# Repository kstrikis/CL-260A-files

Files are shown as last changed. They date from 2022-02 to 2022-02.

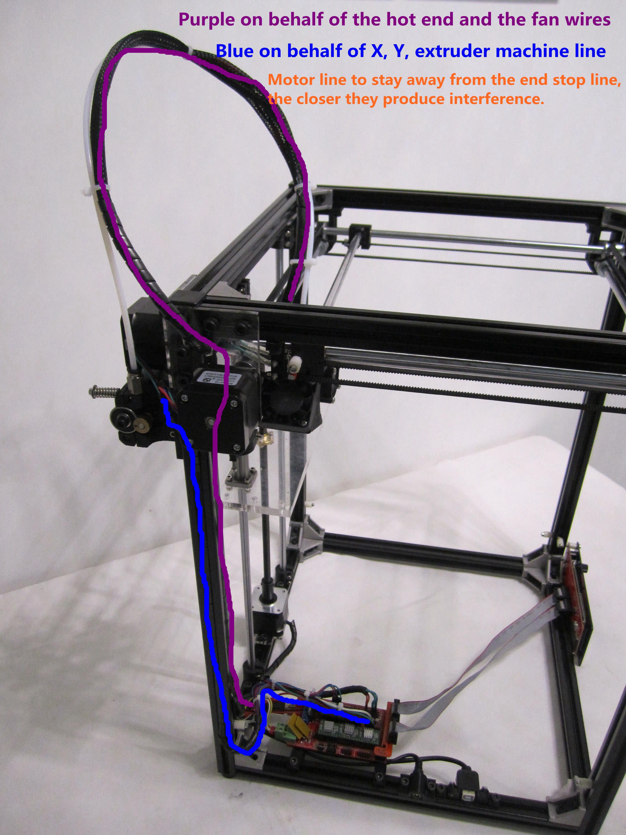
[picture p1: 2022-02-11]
CL-260 manual (original information pack)/Assemble the tutorial/photo/4.JPG

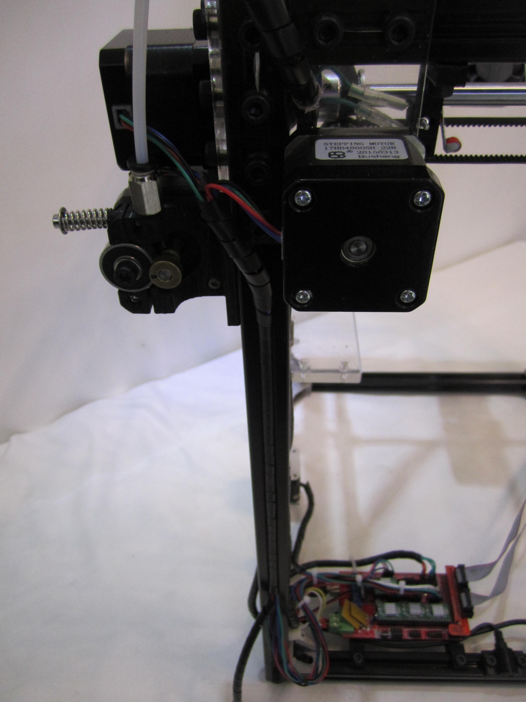
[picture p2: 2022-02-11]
CL-260 manual (original information pack)/Assemble the tutorial/photo/11.JPG

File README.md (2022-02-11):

# CL-260A-files
Files and notes for running an Ultimaker 2 clone 3D printer

Thanks to SirGeekALot for most of the Marlin tweaks.
Notably, my extruder PID settings are very different from his, though.
So you should find your own, with M303 C8 E0 S205 U1
| Original					 | SirGeekALot					 | Mine |
| :---: | :---: | :---: |
| #define  DEFAULT_Kp 22.2	| #define  DEFAULT_Kp 29.79	| #define DEFAULT_Kp  14.06 |
| #define  DEFAULT_Ki 1.08	| #define  DEFAULT_Ki 2.31	| #define DEFAULT_Ki 0.64 |
| #define  DEFAULT_Kd 114	  | #define  DEFAULT_Kd 95.90	| #define DEFAULT_Kd  76.44 |

### To send the tweaked Marlin firmware to your CL-260A:

0. Ensure you have the same hardware, including:
Arduino Mega 2560  
RAMPS 1.4 board  
Heated bed  
A4988 stepper drivers  
128 x 64 LCD screen <-- If you do not have this, comment out line 2378 in Configuration.h:  
    //#define REPRAP_DISCOUNT_FULL_GRAPHIC_SMART_CONTROLLER

1. Install drivers for the CH340 USB-serial chip
	Copies of the driver files are in "CH340 drivers"
	The OEM's drivers page: http://www.wch.cn/download/CH341SER_EXE.html

2. Install Arduino IDE
	https://www.arduino.cc/en/software

3. Test the connection to the Arduino by uploading the blink example program

4. Download Marlin 2.0.x: https://github.com/MarlinFirmware/Marlin
   I used Marlin 2.0.9.3

5. Replace Configuration.h and Configuration_adv.h

6. Run Marlin.ino

7. Upload. This takes several minutes.

8. Run M303 C8 E0 S205 U1 to find your own extruder PID settings.  
	This already saves the settings in EEPROM, but better to keep a copy.  
	Watch the terminal near completion so the temp sensor readings
	don't push the PID tuning output past the end of the log
	before you can read them

9. Add your PID settings to your own copy of Configuration.h

### To use import the Cura settings:

1. Install Cura
	https://ultimaker.com/software/ultimaker-cura
	I used Cura 4.13.1
  
2. Help -> Show Configuration Folder

3. Copy all the files from "cura" into your configuration folder

4. Note that my starting G-code includes a "brush wipe" step
  where you may strap a toothbrush in that corner to wipe the
  nozzle over it before each print.

### CL-260 manual (original information pack) is what the manufacturer provided.
It uses Marlin 1.x (incompatible with 2.x), has a similarly incompatible Cura file.  
They suggest Repetier but with a Raspberry Pi and Octoprint you can untether
the printer from your computer.

### Other changes:
Better 24V power supply  
    Cover for PSU: https://www.thingiverse.com/thing%3a119109  
        https://web.archive.org/web/20161110102835/http://www.thingiverse.com/thing:119109   
        Here is a similar one: https://www.thingiverse.com/thing:40377  
    Bracket for PSU: CL-26_PSU_Bracket.stl  
Add grounding wires to the frame  
Add spool holder that fits onto provided bolt: m5-spool-holder.stl  
Case for 12864 LCD screen: https://www.thingiverse.com/search?q=12864+case&type=things&sort=relevant  
Longer ribbon cables to mount LCD screen on top T-slot frame  
Messy wiring  
Piece of tempered glass that is almost the right size  

### Potential changes:
* Use RAMPS 1.6 board  
* Use better stepper drivers. quieter operation, maybe smoother  
* DRV8825 - do not use. requires TL smoother for use at low speed  
* TMC2130  
* TMC2208  
* TMC2209 - less hot than TMC2208.  
  Support for sensorless homing! Very cool. Maybe it puts too much force on z-axis, though;  
  you don't want to delevel the bed or damage the bed or nozzle.  
  Still, it could potentially allow mesh bed leveling.  
  The TMC2209 uses UART mode for sensorless homing, to use it will require some wiring.  
  You can use one-to-many wiring, where all the stepper motors share a bus and are configured with unique 2-bit addresses  
  The extruder should be run with spreadCycle, axis motors run with stealthChop  
  These two modes are configured by bringing a couple pins to VCC, ground, or leaving them open on the driver

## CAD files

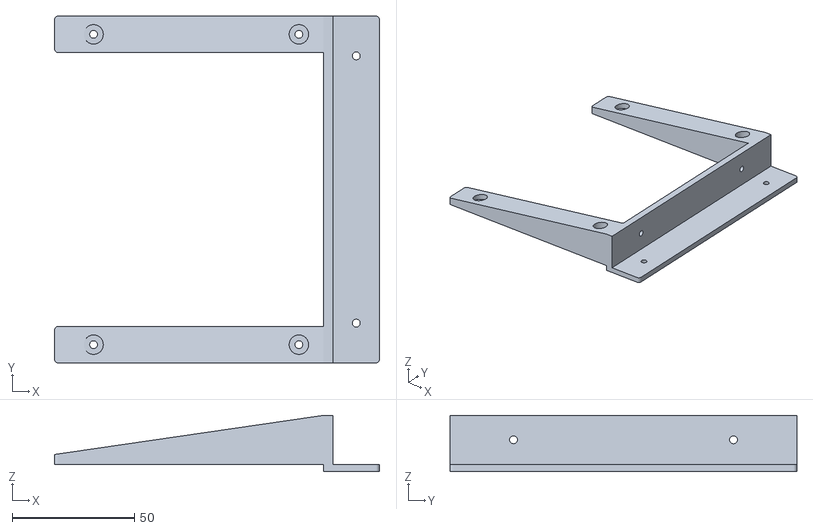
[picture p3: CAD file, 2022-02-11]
parts/CL-26_PSU_Bracket.stl
133.0 x 142.0 x 23.0

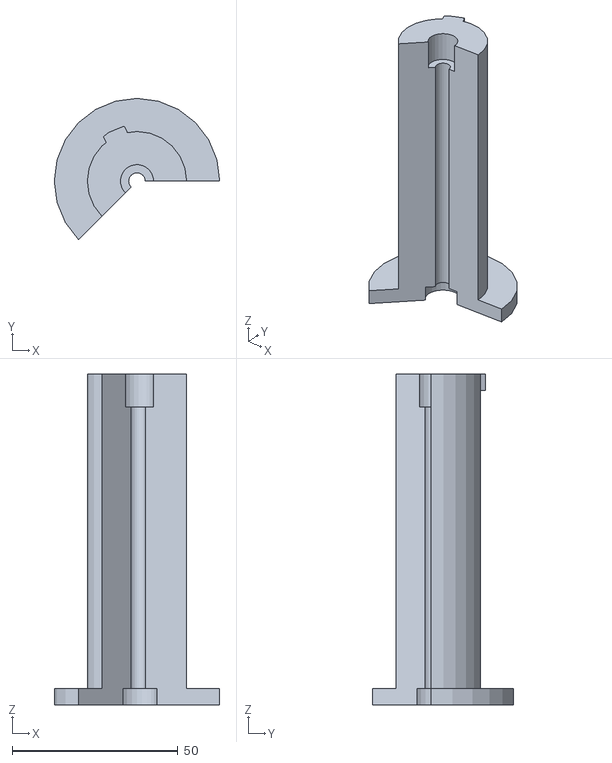
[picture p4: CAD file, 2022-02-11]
parts/m5-spool-holder.stl
50.0 x 42.7 x 100.0

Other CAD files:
parts/m5-spool-holder.skp

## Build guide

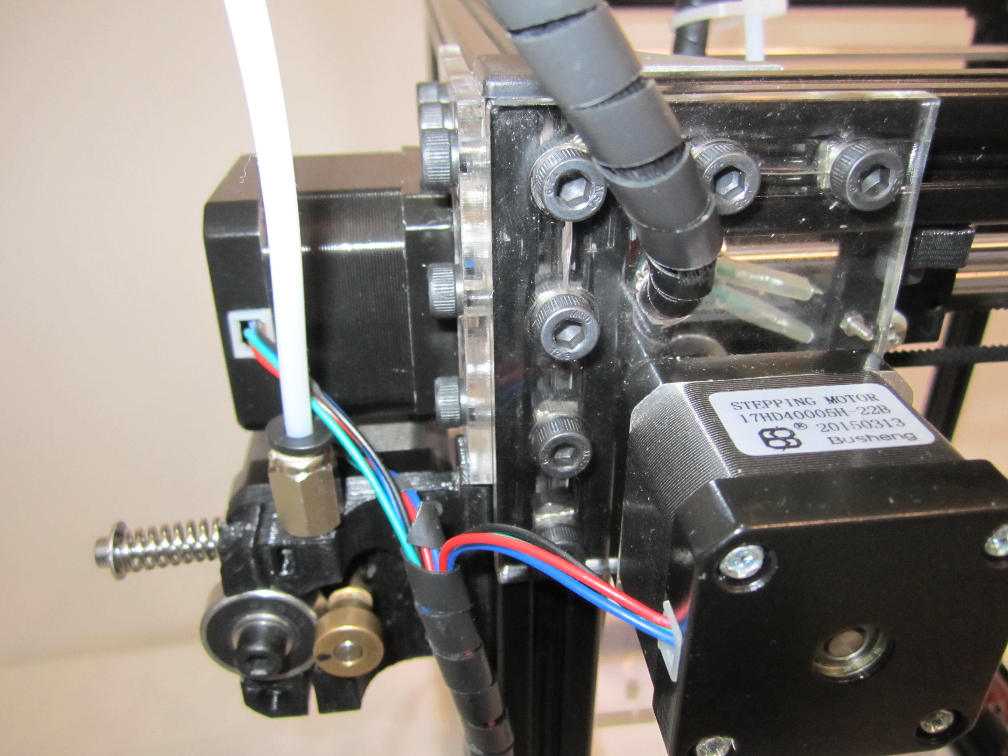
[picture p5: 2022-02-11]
CL-260 manual (original information pack)/Assemble the tutorial/photo/9.JPG

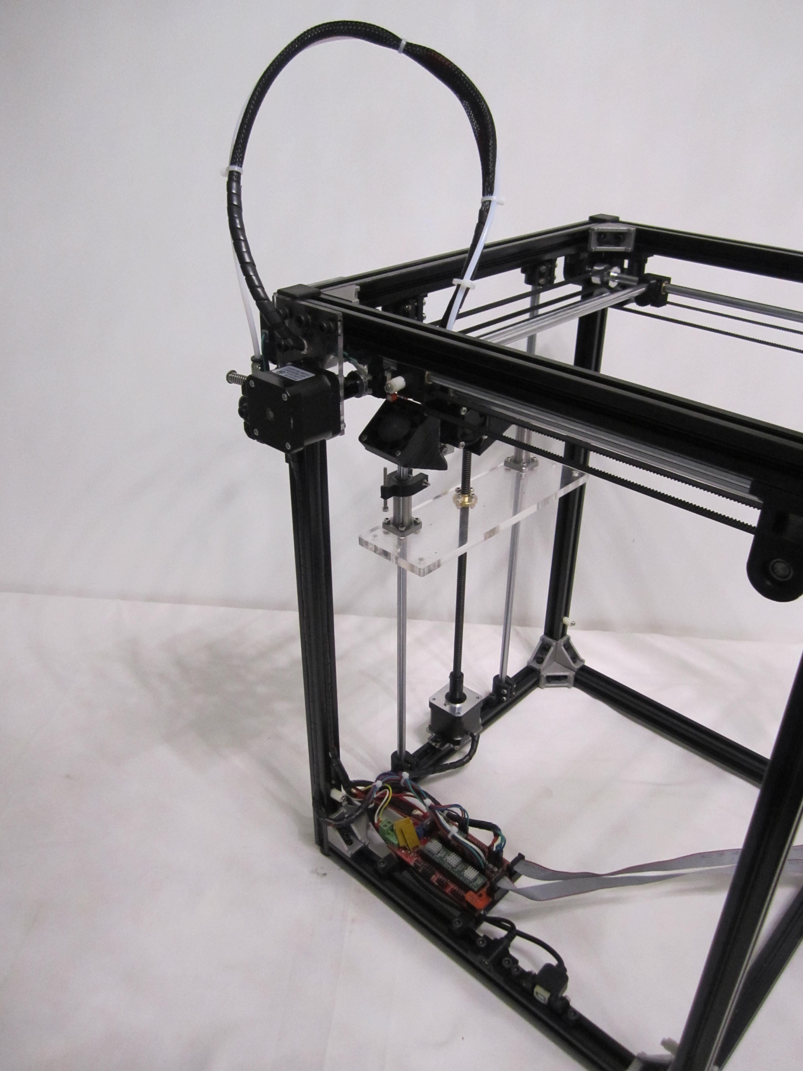
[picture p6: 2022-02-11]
CL-260 manual (original information pack)/Assemble the tutorial/photo/3.JPG

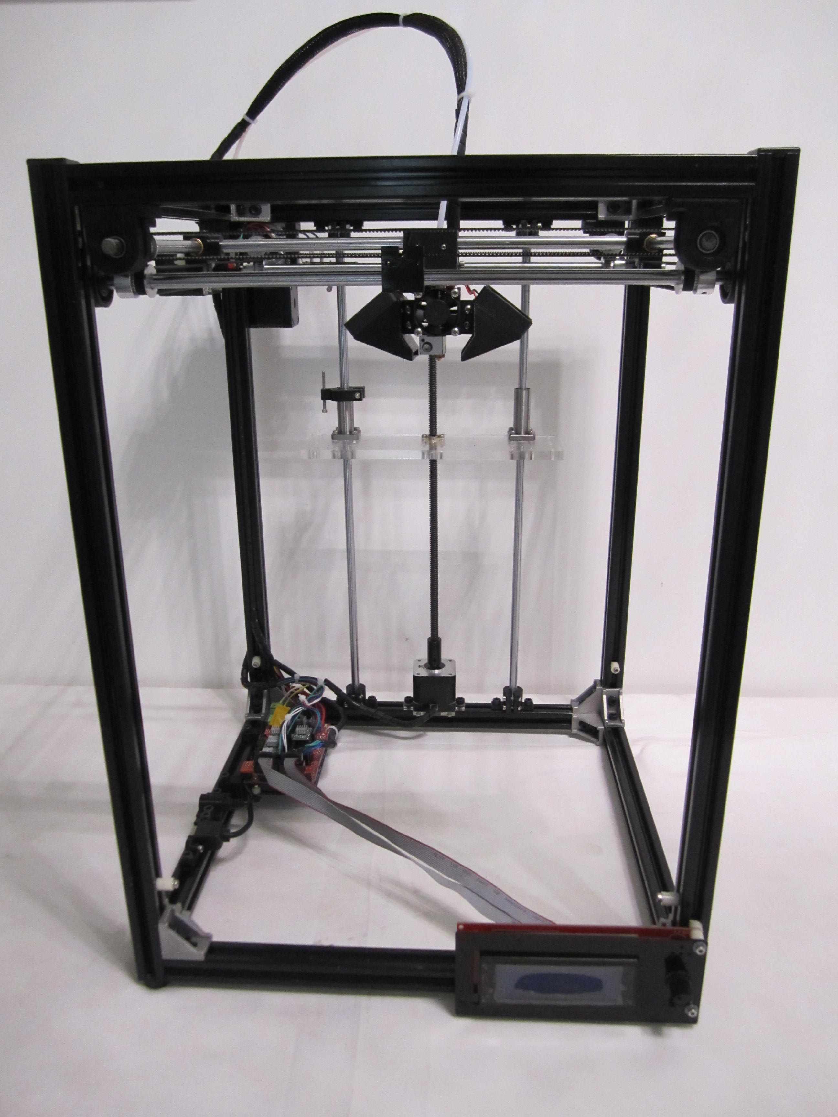
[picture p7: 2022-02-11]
CL-260 manual (original information pack)/Assemble the tutorial/photo/1.JPG

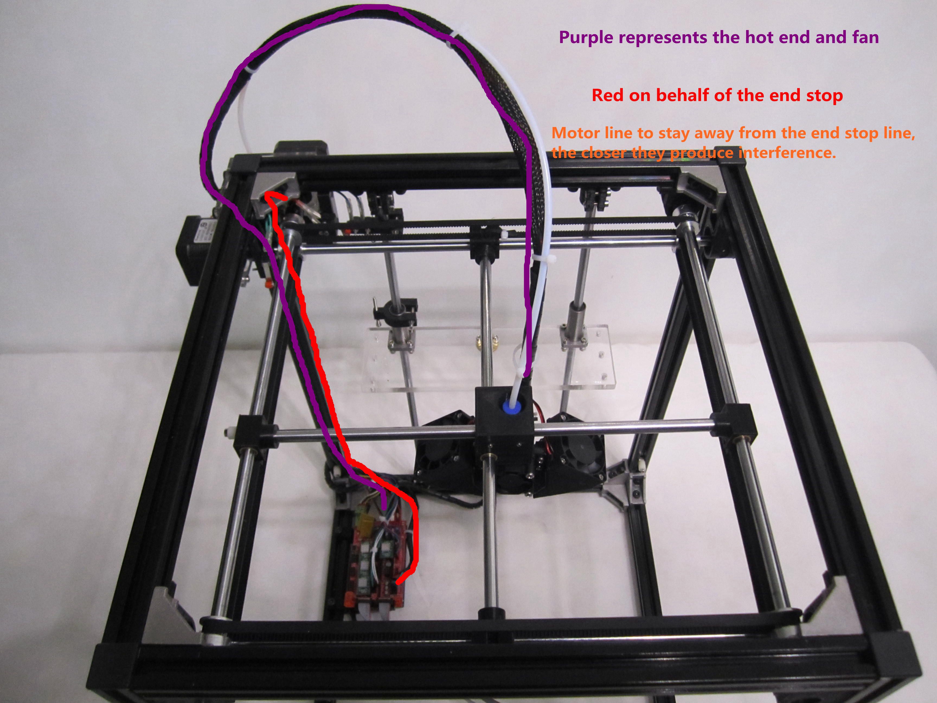
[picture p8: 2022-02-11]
CL-260 manual (original information pack)/Assemble the tutorial/photo/2.JPG

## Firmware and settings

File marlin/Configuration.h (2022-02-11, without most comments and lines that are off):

#pragma once
#define CONFIGURATION_H_VERSION 02000903
#define STRING_CONFIG_H_AUTHOR "(none, CL-260)" // Who made the changes.
#define SHOW_BOOTSCREEN
  #define MOTHERBOARD BOARD_RAMPS_14_EFB
#define SERIAL_PORT 0
#define BAUDRATE 250000
#define CUSTOM_MACHINE_NAME "CL-260A"
#if LINEAR_AXES >= 4
  #define AXIS4_NAME 'A' // :['A', 'B', 'C', 'U', 'V', 'W']
#endif
#if LINEAR_AXES >= 5
  #define AXIS5_NAME 'B' // :['A', 'B', 'C', 'U', 'V', 'W']
#endif
#if LINEAR_AXES >= 6
  #define AXIS6_NAME 'C' // :['A', 'B', 'C', 'U', 'V', 'W']
#endif
#define EXTRUDERS 1
#define DEFAULT_NOMINAL_FILAMENT_DIA 1.75
#define TEMP_SENSOR_0 1
#define TEMP_SENSOR_1 0
#define TEMP_SENSOR_2 0
#define TEMP_SENSOR_3 0
#define TEMP_SENSOR_4 0
#define TEMP_SENSOR_5 0
#define TEMP_SENSOR_6 0
#define TEMP_SENSOR_7 0
#define TEMP_SENSOR_BED 1
#define TEMP_SENSOR_PROBE 0
#define TEMP_SENSOR_CHAMBER 0
#define TEMP_SENSOR_COOLER 0
#define TEMP_SENSOR_BOARD 0
#define TEMP_SENSOR_REDUNDANT 0
#define DUMMY_THERMISTOR_998_VALUE  25
#define DUMMY_THERMISTOR_999_VALUE 100
#define TEMP_RESIDENCY_TIME         10  // (seconds) Time to wait for hotend to "settle" in M109
#define TEMP_WINDOW                  1  // (°C) Temperature proximity for the "temperature reached" timer
#define TEMP_HYSTERESIS              6  // (°C) Temperature proximity considered "close enough" to the target--from 3 to 6
#define TEMP_BED_RESIDENCY_TIME     10  // (seconds) Time to wait for bed to "settle" in M190
#define TEMP_BED_WINDOW              1  // (°C) Temperature proximity for the "temperature reached" timer
#define TEMP_BED_HYSTERESIS          3  // (°C) Temperature proximity considered "close enough" to the target
#define TEMP_CHAMBER_RESIDENCY_TIME 10  // (seconds) Time to wait for chamber to "settle" in M191
#define TEMP_CHAMBER_WINDOW          1  // (°C) Temperature proximity for the "temperature reached" timer
#define TEMP_CHAMBER_HYSTERESIS      3  // (°C) Temperature proximity considered "close enough" to the target
#if TEMP_SENSOR_REDUNDANT
  #define TEMP_SENSOR_REDUNDANT_SOURCE    E1  // The sensor that will provide the redundant reading.
  #define TEMP_SENSOR_REDUNDANT_TARGET    E0  // The sensor that we are providing a redundant reading for.
  #define TEMP_SENSOR_REDUNDANT_MAX_DIFF  10  // (°C) Temperature difference that will trigger a print abort.
#endif
#define HEATER_0_MINTEMP   5
#define HEATER_1_MINTEMP   5
#define HEATER_2_MINTEMP   5
#define HEATER_3_MINTEMP   5
#define HEATER_4_MINTEMP   5
#define HEATER_5_MINTEMP   5
#define HEATER_6_MINTEMP   5
#define HEATER_7_MINTEMP   5
#define BED_MINTEMP        5
#define CHAMBER_MINTEMP    5
#define HEATER_0_MAXTEMP 275
#define HEATER_1_MAXTEMP 275
#define HEATER_2_MAXTEMP 275
#define HEATER_3_MAXTEMP 275
#define HEATER_4_MAXTEMP 275
#define HEATER_5_MAXTEMP 275
#define HEATER_6_MAXTEMP 275
#define HEATER_7_MAXTEMP 275
#define BED_MAXTEMP      150
#define CHAMBER_MAXTEMP  60
#define HOTEND_OVERSHOOT 15   // (°C) Forbid temperatures over MAXTEMP - OVERSHOOT
#define BED_OVERSHOOT    10   // (°C) Forbid temperatures over MAXTEMP - OVERSHOOT
#define COOLER_OVERSHOOT  2   // (°C) Forbid temperatures closer than OVERSHOOT
#define PIDTEMP
#define BANG_MAX 255     // Limits current to nozzle while in bang-bang mode; 255=full current
#define PID_MAX BANG_MAX // Limits current to nozzle while PID is active (see PID_FUNCTIONAL_RANGE below); 255=full current
#define PID_K1 0.95      // Smoothing factor within any PID loop
    #define DEFAULT_Kp  14.06 //originally 22.20. from autotune:
    #define DEFAULT_Ki   0.64 // 2.31  // M303 C8 E0 S205 U1
    #define DEFAULT_Kd  76.44 // 114   // C8 eight cycles E0 extruder0 S205 temp U1 save to EEPROM
#define MAX_BED_POWER 255 // limits duty cycle to bed; 255=full current
#define MAX_CHAMBER_POWER 255 // limits duty cycle to chamber heater; 255=full current
  #define PID_FUNCTIONAL_RANGE 10 // If the temperature difference between the target temperature and the actual temperature
#define PREVENT_COLD_EXTRUSION
#define EXTRUDE_MINTEMP 170
#define PREVENT_LENGTHY_EXTRUDE
#define EXTRUDE_MAXLENGTH 200
#define THERMAL_PROTECTION_HOTENDS // Enable thermal protection for all extruders
#define THERMAL_PROTECTION_BED     // Enable thermal protection for the heated bed
#define THERMAL_PROTECTION_CHAMBER // Enable thermal protection for the heated chamber
#define THERMAL_PROTECTION_COOLER  // Enable thermal protection for the laser cooling
#define USE_XMIN_PLUG
#define USE_ZMIN_PLUG
#define USE_YMAX_PLUG
#define ENDSTOPPULLUPS
#define X_MIN_ENDSTOP_INVERTING true // Set to true to invert the logic of the endstop.
#define Y_MIN_ENDSTOP_INVERTING true // Set to true to invert the logic of the endstop.
#define Z_MIN_ENDSTOP_INVERTING true // Set to true to invert the logic of the endstop.
#define I_MIN_ENDSTOP_INVERTING false // Set to true to invert the logic of the endstop.
#define J_MIN_ENDSTOP_INVERTING false // Set to true to invert the logic of the endstop.
#define K_MIN_ENDSTOP_INVERTING false // Set to true to invert the logic of the endstop.
#define X_MAX_ENDSTOP_INVERTING true // Set to true to invert the logic of the endstop.
#define Y_MAX_ENDSTOP_INVERTING true // Set to true to invert the logic of the endstop.
#define Z_MAX_ENDSTOP_INVERTING true // Set to true to invert the logic of the endstop.
#define I_MAX_ENDSTOP_INVERTING false // Set to true to invert the logic of the endstop.
#define J_MAX_ENDSTOP_INVERTING false // Set to true to invert the logic of the endstop.
#define K_MAX_ENDSTOP_INVERTING false // Set to true to invert the logic of the endstop.
#define Z_MIN_PROBE_ENDSTOP_INVERTING false // Set to true to invert the logic of the probe.
#define X_DRIVER_TYPE  A4988
#define Y_DRIVER_TYPE  A4988
#define Z_DRIVER_TYPE  A4988
#define E0_DRIVER_TYPE A4988
#define DEFAULT_AXIS_STEPS_PER_UNIT   {80,80,1600,145}  // SirGeekALot: CL-260A settings {x,y,z,e} for the
#define DEFAULT_MAX_FEEDRATE          { 300, 300, 5, 25 }
#define DEFAULT_MAX_ACCELERATION      { 3000, 3000, 100, 10000 }
#define DEFAULT_ACCELERATION          3000    // X, Y, Z and E acceleration for printing moves
#define DEFAULT_RETRACT_ACCELERATION  3000    // E acceleration for retracts
#define DEFAULT_TRAVEL_ACCELERATION   3000    // X, Y, Z acceleration for travel (non printing) moves
#define DEFAULT_EJERK    5.0  // May be used by Linear Advance
  #define JUNCTION_DEVIATION_MM 0.013 // (mm) Distance from real junction edge
  #define JD_HANDLE_SMALL_SEGMENTS    // Use curvature estimation instead of just the junction angle
#define Z_MIN_PROBE_USES_Z_MIN_ENDSTOP_PIN
#define NOZZLE_TO_PROBE_OFFSET { 10, 10, 0 }
#define PROBING_MARGIN 10
#define XY_PROBE_FEEDRATE (133*60)
#define Z_PROBE_FEEDRATE_FAST (4*60)
#define Z_PROBE_FEEDRATE_SLOW (Z_PROBE_FEEDRATE_FAST / 2)
#define Z_CLEARANCE_DEPLOY_PROBE   10 // Z Clearance for Deploy/Stow
#define Z_CLEARANCE_BETWEEN_PROBES  5 // Z Clearance between probe points
#define Z_CLEARANCE_MULTI_PROBE     5 // Z Clearance between multiple probes
#define Z_PROBE_LOW_POINT          -2 // Farthest distance below the trigger-point to go before stopping
#define Z_PROBE_OFFSET_RANGE_MIN -20
#define Z_PROBE_OFFSET_RANGE_MAX 20
#define X_ENABLE_ON 0
#define Y_ENABLE_ON 0
#define Z_ENABLE_ON 0
#define E_ENABLE_ON 0 // For all extruders
#define DISABLE_X false
#define DISABLE_Y false
#define DISABLE_Z false
#define DISABLE_E false             // Disable the extruder when not stepping
#define DISABLE_INACTIVE_EXTRUDER   // Keep only the active extruder enabled
#define INVERT_X_DIR false
#define INVERT_Y_DIR true
#define INVERT_Z_DIR false
#define INVERT_E0_DIR true
#define INVERT_E1_DIR false
#define INVERT_E2_DIR false
#define INVERT_E3_DIR false
#define INVERT_E4_DIR false
#define INVERT_E5_DIR false
#define INVERT_E6_DIR false
#define INVERT_E7_DIR false
#define X_HOME_DIR -1
#define Y_HOME_DIR  1
#define Z_HOME_DIR -1
#define X_BED_SIZE 220
#define Y_BED_SIZE 220
#define X_MIN_POS 0
#define Y_MIN_POS 0
#define Z_MIN_POS 0
#define X_MAX_POS X_BED_SIZE
#define Y_MAX_POS Y_BED_SIZE
#define Z_MAX_POS 260
#define MIN_SOFTWARE_ENDSTOPS
  #define MIN_SOFTWARE_ENDSTOP_X
  #define MIN_SOFTWARE_ENDSTOP_Y
  #define MIN_SOFTWARE_ENDSTOP_Z
  #define MIN_SOFTWARE_ENDSTOP_I
  #define MIN_SOFTWARE_ENDSTOP_J
  #define MIN_SOFTWARE_ENDSTOP_K
#define MAX_SOFTWARE_ENDSTOPS
  #define MAX_SOFTWARE_ENDSTOP_X
  #define MAX_SOFTWARE_ENDSTOP_Y
  #define MAX_SOFTWARE_ENDSTOP_Z
  #define MAX_SOFTWARE_ENDSTOP_I
  #define MAX_SOFTWARE_ENDSTOP_J
  #define MAX_SOFTWARE_ENDSTOP_K
#define HOMING_FEEDRATE_MM_M { (50*60), (50*60), (4*60) }
#define VALIDATE_HOMING_ENDSTOPS
#define EEPROM_CHITCHAT       // Give feedback on EEPROM commands. Disable to save PROGMEM.
#define EEPROM_BOOT_SILENT    // Keep M503 quiet and only give errors during first load
#define HOST_KEEPALIVE_FEATURE        // Disable this if your host doesn't like keepalive messages
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

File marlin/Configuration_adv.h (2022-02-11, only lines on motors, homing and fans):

#define E0_AUTO_FAN_PIN -1
#define E1_AUTO_FAN_PIN -1
#define E2_AUTO_FAN_PIN -1
#define E3_AUTO_FAN_PIN -1
#define E4_AUTO_FAN_PIN -1
#define E5_AUTO_FAN_PIN -1
#define E6_AUTO_FAN_PIN -1
#define E7_AUTO_FAN_PIN -1
#define CHAMBER_AUTO_FAN_PIN -1
#define COOLER_AUTO_FAN_PIN -1
#define COOLER_FAN_PIN -1
#define HOMING_BUMP_MM      { 5, 5, 2 }       // (mm) Backoff from endstops after first bump
#define HOMING_BUMP_DIVISOR { 2, 2, 4 }       // Re-Bump Speed Divisor (Divides the Homing Feedrate)
#define MICROSTEP_MODES { 16, 16, 16, 16, 16, 16 } // [1,2,4,8,16]

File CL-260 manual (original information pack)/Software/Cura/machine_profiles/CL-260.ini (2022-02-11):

[machine]
machine_name = CL-260
machine_type = CL-260
machine_width = 220
machine_depth = 220
machine_height = 260
machine_center_is_zero = False
has_heated_bed = False
gcode_flavor = RepRap (Marlin/Sprinter)
extruder_amount = 1
serial_baud = 115200

[profile]
layer_height = 0.2
wall_thickness = 1.2
retraction_enable = True
solid_layer_thickness = 0.6
fill_density = 20
nozzle_size = 0.4
print_speed = 50
print_temperature = 220
support = None
platform_adhesion = None
filament_diameter = 1.75
filament_flow = 100.0
retraction_speed = 120
retraction_amount = 5
retraction_min_travel = 1.5
retraction_combing = All
retraction_minimal_extrusion = 0.02
retraction_hop = 0.0
bottom_thickness = 0.3
layer0_width_factor = 100
object_sink = 0
travel_speed = 80
bottom_layer_speed = 20
infill_speed = 60
solidarea_speed = 20
inset0_speed = 30
insetx_speed = 40
cool_min_layer_time = 5
fan_enabled = True
skirt_line_count = 1
skirt_gap = 3.0
skirt_minimal_length = 150.0
fan_full_height = 1.5
fan_speed = 50
fan_speed_max = 50
cool_min_feedrate = 10
cool_head_lift = False
solid_top = True
solid_bottom = True
fill_overlap = 15
perimeter_before_infill = True
support_type = Lines
support_angle = 60
support_fill_rate = 10
support_xy_distance = 0.7
support_z_distance = 0.2
spiralize = False
simple_mode = False
brim_line_count = 20
raft_margin = 5
raft_line_spacing = 1.0
raft_base_thickness = 0.3
raft_base_linewidth = 0.7
raft_interface_thickness = 0.2
raft_interface_linewidth = 0.2
raft_airgap = 0.22
raft_surface_layers = 2
fix_horrible_union_all_type_a = True
fix_horrible_union_all_type_b = False
fix_horrible_use_open_bits = False
fix_horrible_extensive_stitching = False
plugin_config = (lp1
	.
object_center_x = -1
object_center_y = -1

[alterations]
start.gcode = 
	; -- START GCODE --
	;Sliced at: {day} {date} {time}
	;Basic settings: Layer height: {layer_height} Walls: {wall_thickness} Fill: {fill_density}
	;Print time: {print_time}
	;Filament used: {filament_amount}m {filament_weight}g
	;Filament cost: {filament_cost}
	;Uncomment to add your own temperature line
	;M109 S{print_temperature}
	;Uncomment to add your own bed temperature line
	;M190 S{print_bed_temperature}
	G21                     ;metric values
	G90                     ;absolute positioning
	M107                    ;start with the fan off
	G28 X0 Y220             ;move X/Y to min endstops
	G28 Z0                  ;move Z to min endstops
	G1 Z15.0 F1200          ;move the platform down 15mm
	G92 E0                  ;zero the extruded length
	G1 F200 E22             ;extrude 20mm of feed stock
	G92 E0                  ;zero the extruded length again
	G1 F{travel_speed}
	;Uncomment to put a printing message on LCD screen
	;M117 Printing...
	; -- end of START GCODE --

end.gcode = 
	; -- END GCODE --
	M104 S0                 ;extruder heater off
	M140 S0                 ;Disable heated bed
	G91                     ;relative positioning
	G1 E-20 F300            ;retract the filament a bit before lifting the nozzle, to release some of the pressure
	G90                     ;absolute positioning
	G28 X0 Y220             ;move X/Y to min endstops, so the head is out of the way
	M84                     ;steppers off
	; -- end of END GCODE --

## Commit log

2022-02-11 3d printable parts
    [CL-26_PSU_Bracket.stl, m5-spool-holder.skp, m5-spool-holder.stl]
2022-02-11 initial cura settings
    [CL-260A.global.cfg, ultimaker2_extruder_0+%232.extruder.cfg]
2022-02-11 marlin config files
    [Configuration.h, Configuration_adv.h]

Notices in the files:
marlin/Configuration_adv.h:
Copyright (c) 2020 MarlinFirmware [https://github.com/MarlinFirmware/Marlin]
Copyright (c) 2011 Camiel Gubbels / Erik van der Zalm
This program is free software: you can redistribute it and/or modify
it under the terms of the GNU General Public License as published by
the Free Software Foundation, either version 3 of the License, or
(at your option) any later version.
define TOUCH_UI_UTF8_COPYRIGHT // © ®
